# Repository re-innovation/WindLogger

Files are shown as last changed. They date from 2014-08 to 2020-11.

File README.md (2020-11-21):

# Low Cost Data Logger for Wind Speed Parameters
This repository has the open-source files for a Data Logger for Wind Speed and other small wind turbine parameters.

So far there have been two different versions of this unit:
* Version 1 was released in 2014. This was basic add on shield for the 'DataDuino' (an Arduino based SD card datalogger from www.re-innovation.co.uk)
* Version 2 was released on 2016. This was a surface mount design with additional functions such as solar PV charging.

The Wind Logger was originally designed by Matt Little of www.re-innovation.co.uk
Contact: info@re-innovation.co.uk

Please see: www.re-innovation.co.uk and search for 'wind datalogger' for more details.
Some more details are available here:
https://www.re-innovation.co.uk/docs/wind-datalogger/

The folders in this repository include:
	
* WindLogger_PCB
The PCB files were created in KiCAD PCB design software
These are in Windlogger_PCB
There are the KICAD project files and the GERBER files for both the DataDuino and the Windlogger Shield	

* WindLogger_FIRMWARE
Example code has been written for uploading via the Arduino IDE.

* WindLogger_FIXINGS
The CAD design for fixing system for an anemometer and a wind vane.
These is a work in progress. Originally draw using CorelDraw - I hope to update/convert this soon.
	
* WindLogger_INSTRUCTIONS
These are the instructions in a number of formats and languages.

## Version 1 - 2014
Overview of the design:
  A PCF8563 Real Time Clock is used to timestamp the data.

  Pin D3 is set up to cound pulses from a sensor (such as a anemometer or flow sensor)
 
  Pins D7,D8,D9 are set up to record digital information (0 or 1)
  
  Pins A0 to A3 are set up to record analogue information (0 to 1024)
  
  Each logger has a reference (user adjustable from 00-99).
  
  Data is written to a .csv file created on an SD card.
  
  A new file is created each day. If file alreay present then data is appended.
  
  The file name is created from the reference number and the date in the format:
  
  RXXDXXXX.csv, where RXX is the reference number and DXXXX is the date in the format DDMM. 
  
  Data is stored with human readable headers. Check the Arduino code for these.
  
  You can adjust the parameters of the device using serial commands. These parameters are stored in EEPROM.
  These are:
  * R??E - This will change the reference number to ??
  * T??????E - This will change the time to HHMMSS
  * D??????E - This will change the date to DDMMYY
  * S?????E - This will change the sample period to ????? seconds. Set to 00001 for 1 second data, set to 03600 for 1 hour data. (The minimum is 1 second data. The maximum is 99999 seconds)

## Version 3 - 2016
 
This newer version mainly covers a new circuit board which was designed as a surface mount design. The Code on this board has additional changes, but not too different functionality.

## Version 4 - 2020

This is work in progress. I'm trying to create a better PCB design which will also have WiFi and GPRS/2G connectivity for your data.

The wind speed logging unit is a plug in board onto a data-logging main unit.

##  Data Processing
These are programs to take the data on the SD card and produce nice graphs with it.
This is a work in progress.
https://github.com/re-innovation/CSVviewer

## Changes to do!

* PCF8563 - not accurate enough. Use DS3231 with temperature compensation.
* Add data upload via WiFi
* Add data upload via GPRS

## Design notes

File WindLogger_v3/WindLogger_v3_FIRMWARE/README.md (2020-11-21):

# WindLoggerVersion3 - Arduino Code

  See www.re-innovation.co.uk for information and construction details

  The DataDuino is an Arduino based SD card datalogger.
  A PCF8563 Real Time Clock is used to timestamp the data.

  The logger is based on the Arduino Uno (ATMEGA328P).
  This board option should be selected in the Arduino IDE for programming.

## Features
  Counts pulses from a sensor (such as a anemometer or flow sensor)
  These are pulses are averaged into a wind speed.
  
  We also keep a record of the maximum in the averaging period.
  For turbulence measurement 
  
  Each logger has a reference number (user adjustable).
  
  Data is written to a .csv file created on an SD card.
  
  A new file is created each day. If file already present then data is appended.
  The file name is created from the current date in the format DXXXXXX.csv, where DXXXXXX is the date in the format YYMMDD. 
  
  Data is stored with a human readable header line at the start of the file.

## Using the code

  The code is a standard Arduino application. You can place the repository inside your Arduino sketches directory. 

  In order to build the software, additional arduino libraries are required.
  
  ### Logger configuration

  In app.h, you can set which fields are recorded.
  Each field has a READ define (for example READ_TEMPERATURE).
  To enable recording of this field, set this define to 1.
  To disable recording of this field, set this define to 0.
  
  ### Adding new fields

  To add a new field to the logger software (for example pressure):
  1. Create a define in app.h that will enable/disable the new field (for example READ_PRESSURE)
  2. Create the module .cpp and .h files. In the .h file, define the headers, e.g.

  ```
  #if READ_PRESSURE == 1
  #define PRESSURE_HEADERS "Pressure mb, "
  #else
  #define PRESSURE_HEADERS ""
  #endif
  ```

  3. In sd.cpp:
    1. Add the header entry to the s_pstr_headers string in the desired position. Be sure to add a trailing slash as per the exisiting entries.
    2. Find the write_configurable_fields function.
      * Add the necessary lines of code to write the new data string to the accumulator.
      * Ensure you surround the new code with ifdef...endif for the field.
      * Ensure you include the line to add a comma before the data.
      For example:

  ```
  #if READ_PRESSURE == 1
  accum->writeChar(comma);
  PRESS_WritePressureToBuffer(accum);
  #endif

  ```

### Required libraries:
  ####[https://github.com/GreyGnome/EnableInterrupt](EnableInterrupt by Mike Schwager)

  On Arduino versions > 1.6.2 this library can be installed via the Library Manager. Search for 'EnableInterrupt' in the manager.

  The WindLogger software is built with EnableInterrupt v0.9.4. Later versions may not be supported.

  ####[https://github.com/greiman/SdFat](SfFat by William Greiman)

  Download the repository from GitHub and copy the 'SdFat' folder to your local Arduino libraries folder.

  ####[http://playground.arduino.cc/Main/RTC-PCF8563](RTC-PCF8563 by Joe Robertson)

  Follow the 'Download, install and import' instructions on that page.

  #### Libraries in this repository

  As an alternative to download the libraries individually, this repository contains suitable versions of each library. Unzip "3rd-party-libraries.zip" into your local Arduino libraries folder.

## Calibrate Mode

  In calibrate mode you can adjust the parameters of the device using serial commands.
  These parameters are stored in device EEPROM so they will be saved if the logger is turned off.
  
  The serial commands are:

  "T??????E"
  
  This will change the time to HHMMSS
  
  "D??????E"
  
  This will change the date to DDMMYY
  
  "S?????E"
  
  This will change the sample period to ????? seconds. Set to 00001 for 1 second data, set to 03600 for 1 hour data.
  The minimum is 1 second data. The maximum is 99999 seconds
  
  "R??E"
  
  This will change the logger reference to ??. 
  
  "OE"
  
  This will take the current reading and write it to the current offset.
  
  "V1???E" &  "V2???E"
  
  These select the two resistor values from the resistor potential divider.
  Values are in k Ohm.
  
  R1 is the top resistor, R2 is the lower resistor.
  
  "I???E"
  
  This sets the current gain value, in mV/A

  "W1E" or "W0E" 
  
  "W1E" sets the windwave potentiometer to be on the HIGH side of the potential divider.
  "W0E" sets the windwave potentiometer to be on the LOW side of the potential divider.

## Pin Assignments
  
  D0 - Rx Serial Data
  
  D1 - Tx Serial Data
  
  D2 - RTC interrupt (1 second pulses)
  
  D3 - Anemometer 1 (pulse interrupt) (& Power to External Unit - eg GSM)
  
  D4 - LED DATA output
  
  D5 - Anemometer 2 (pulse interrupt)
  
  D6 - Calibrate Switch (pull LOW to set)
  
  D7 - Rx_GSM
  
  D8 - Tx_GSM
  
  D9 - Card Detect (SD)
  
  D10 - Chip Select - SD card
  
  D11 - MOSI SD card
  
  D12 - MISO SD card
  
  D13 - SPI CLock SD card
  
  A0 - Wind Vane measurement with 10k pull-down
  
  A1 - Internal battery voltage measurement (from potential divider)
  
  A2 - External voltage measurement (with potential divider) 0-40V DC
  
  A3 - Current measurement
  
  A4 - SDA - I2C connection to RTC
  
  A5 - SCK - I2C connection to RTC

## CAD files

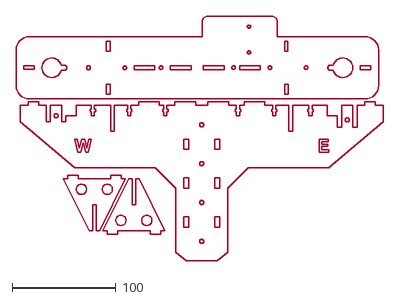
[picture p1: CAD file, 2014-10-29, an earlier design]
WindLogger_v1/WindLogger_v1_FIXINGS/2_10_14_Wind_Logger_Anemometer_Fixing_no_measurements.dxf
354.2 x 236.1

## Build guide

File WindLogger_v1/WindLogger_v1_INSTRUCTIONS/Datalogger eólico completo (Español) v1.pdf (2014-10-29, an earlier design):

### Datalogger eólico completo:

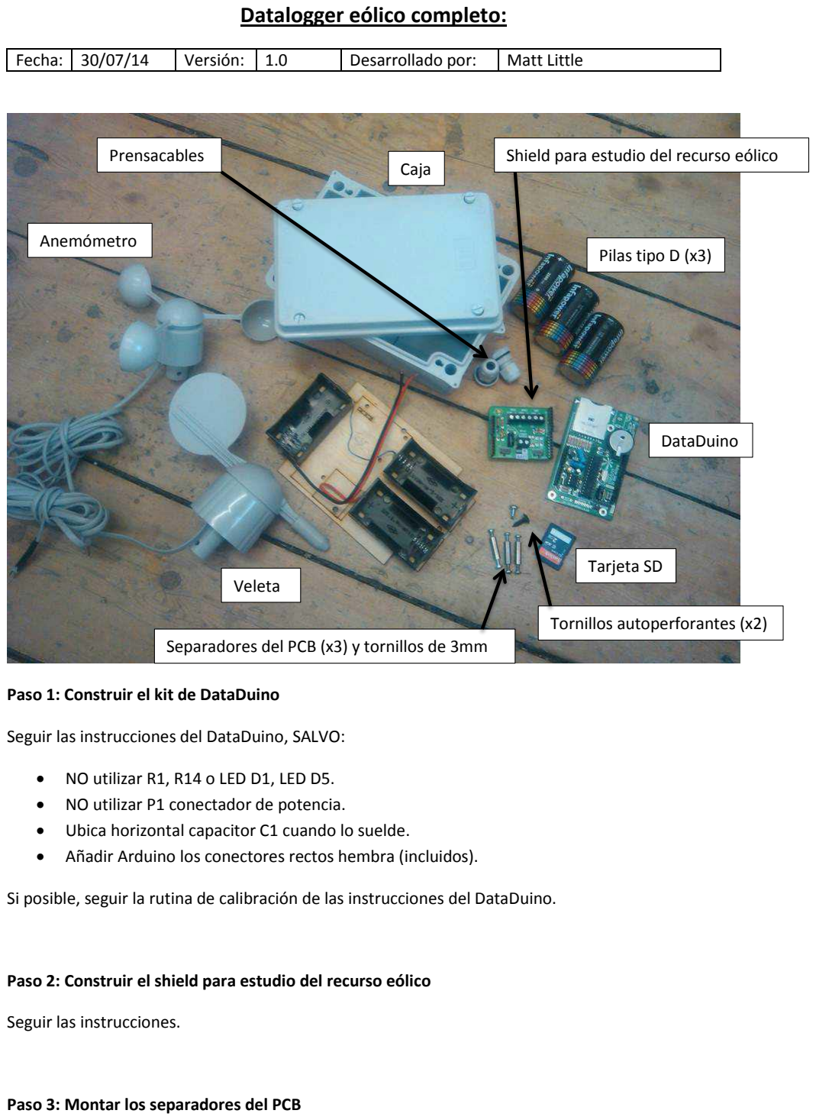
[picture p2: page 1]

Fecha: | 30/07/14 | Versión: | 1.0 | Desarrollado por: | Matt Little

Paso 1: Construir el kit de DataDuino

Seguir las instrucciones del DataDuino, SALVO:

- NO utilizar R1, R14 o LED D1, LED D5.
- NO utilizar P1 conectador de potencia.
- Ubica horizontal capacitor C1 cuando lo suelde.
- Añadir Arduino los conectores rectos hembra (incluidos).

Si posible, seguir la rutina de calibración de las instrucciones del DataDuino.

Paso 2: Construir el shield para estudio del recurso eólico

Seguir las instrucciones.

Paso 3: Montar los separadores del PCB

Caja

Anemómetro

Veleta

Pilas tipo D (x3)

Tarjeta SD

DataDuino

Prensacables | Shield para estudio del recurso eólico

Separadores del PCB (x3) y tornillos de 3mm

Tornillos autoperforantes (x2)

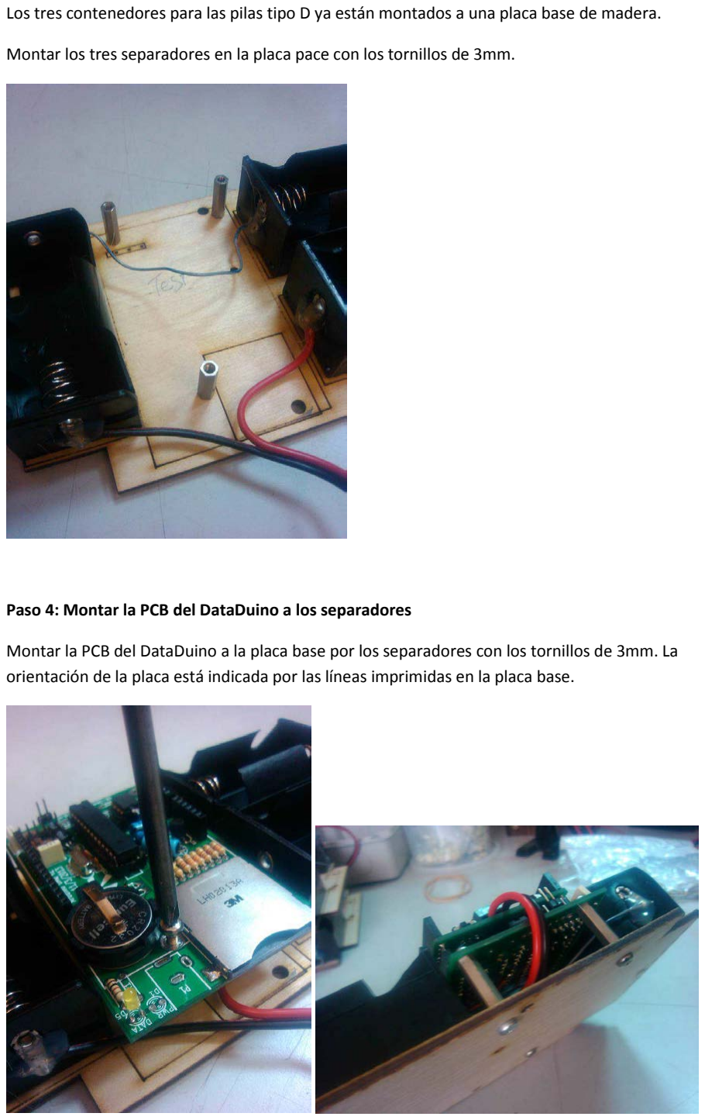
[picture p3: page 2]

Los tres contenedores para las pilas tipo D ya están montados a una placa base de madera.

Montar los tres separadores en la placa pace con los tornillos de 3mm.

Paso 4: Montar la PCB del DataDuino a los separadores

Montar la PCB del DataDuino a la placa base por los separadores con los tornillos de 3mm. La orientación de la placa está indicada por las líneas imprimidas en la placa base.

Paso 5: Montar el PCB del shield para estudio del recurso eólico

El shield para estudio del recurso eólico cabe encima del DataDuino con los conectores rectos hembra. Con cuidado, montarlo al DataDuino, asegurando que están bien alineados todos los conectadores.

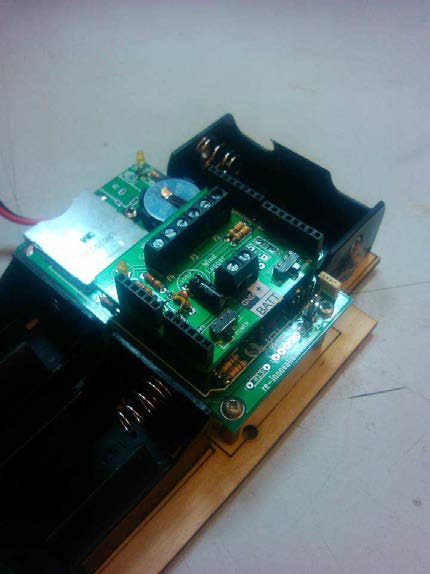
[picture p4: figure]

Paso 6: Conectar la potencia

Sacar 5mm de la aislante del cable de potencia rojo y negro de los tres contenedores de las pilas tipo D y conectarlo en el terminal de potencia (P1).

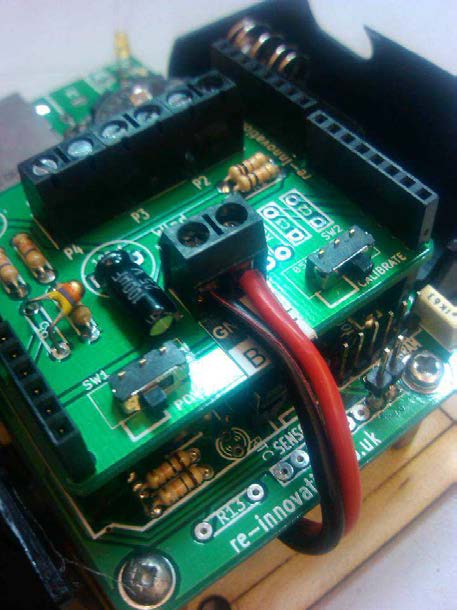
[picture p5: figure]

Paso 7: Montar los prensacables

Montar los prensacables en los agujeros en la caja. Asegurar que están bien apretados.

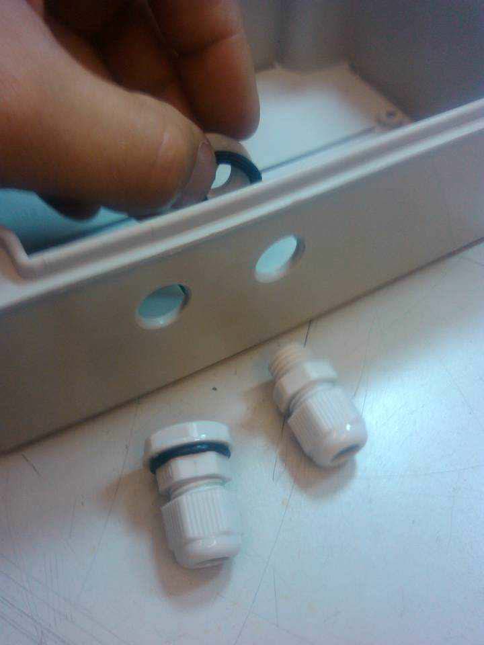
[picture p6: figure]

Paso 8: Introducir la tarjeta SD

Empujar la tarjeta para hacer que entra o sale del leedor de tarjetas SD.

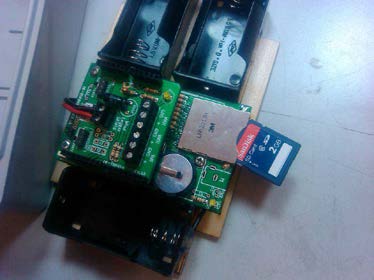
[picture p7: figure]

Paso 9: Montar la placa base en la caja

Montar la placa base de madera en la caja con dos tornillos autoperforantes. Uno tiene una cabeza ancha y entra por uno de los contenedores de pilas tipo D. El otro tiene una cabeza más delgada y cabe entre los dos otros contenedores de pilas.

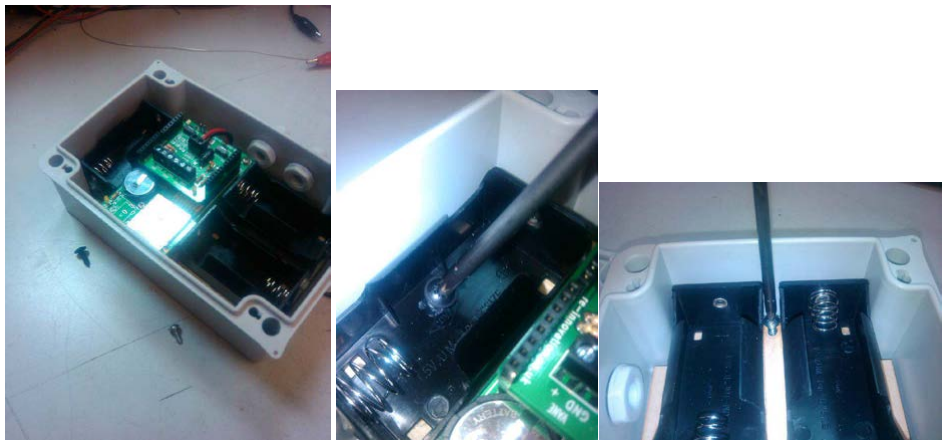
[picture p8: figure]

Paso 10: Conectar el anemómetro y veleta

Cortar los enchufes viejos del anemómetro y la veleta. Asegura que los cables entran por los prensacables.

El anemómetro tiene cables rojo y negro – saca la aislante y conectarlo al terminal Wind 1. La polaridad no importa.

La veleta tiene cuatro cables, pero solo el negro y la verde son necesarios – saca la aislante y conectarlo al terminal Vane. La polaridad no importa.

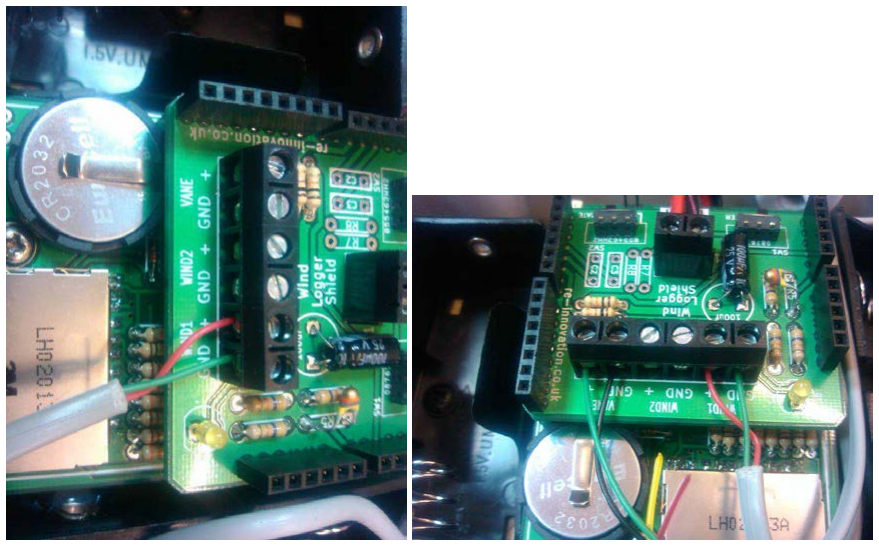
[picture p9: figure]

Paso 11: Poner a prueba con el cable FTDI

NO introducir las pilas. Encender el modo Calibrate (empujarlo el cambio Calibrate hacía el terminal BATT) y enchufar el cable FTDI.

Con una velocidad de transmisión de 115200, debería ver la palabra Calibrate en el terminal serial del IDE Arduino. Para más detalle, consultar las instrucciones del DataDuino.

Corregir la fecha, hora, numero de referencia y tiempo de medición.

Apagar modo Calibrate con el mismo cambio (empujarlo hacía los conectores rectos hembra) – el LED debería luminar una vez cada medición.

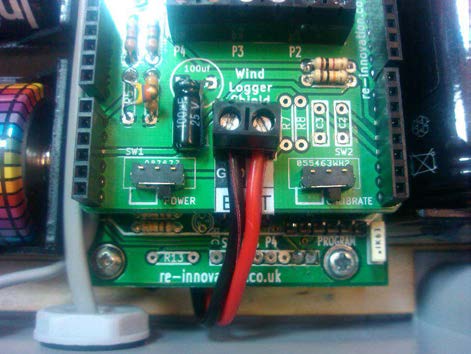
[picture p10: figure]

Paso 12: Introducir las pilas tipo D y encender

Sacar el cable FDTI y asegurar que las pilas tienen las polaridades correctas.

Encenderlo con el cambio Power (empujarlo hacía los terminales BATT)

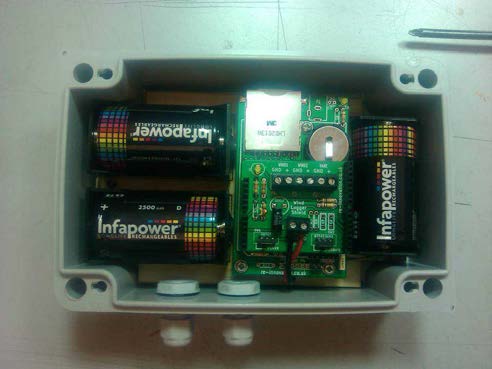
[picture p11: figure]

Paso 13: Instalar anemómetro y veleta

Asegurar que la veleta y anemómetro están instalados a una altura adecuada (si posible, a la misma altura que la turbina) y recordar esta altura.

Nivelar el anemómetro y veleta con un nivel

Orientar la veleta hacía el norte con sartén.

El anemómetro tiene factor de conversión de velocidad del viento a pulsos por segundo de 0.7m/s por Hz. Estos anemómetros no están calibrados en un túnel de viento.

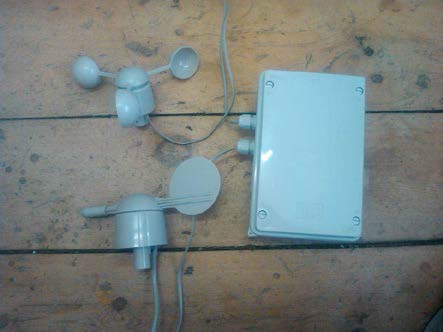
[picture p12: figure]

### Datos de contacto:

Este kit ha sido diseñado y producido por: Renewable Energy Innovation. info@re-innovation.co.uk
www.re-innovation.co.uk
Hopkinson Gallery
21 Street Station
Nottingham
NG7 6PD

Nos gustaría que este kit satisfaga sus necesidades. Si usted no estuviera satisfecho por algún motivo, por favor póngase en contacto con nosotros y le ayudaremos a solucionar el problema. Por favor escribanos a info@re-innovation.co.uk con cualquier pregunta o comentario que quiera hacer. Si falta alguna pieza de su kit por favor envíe un correo electrónico a info@re-innovation.co.uk con todos los detalles, incluyendo dónde se compró el kit.

Puedes encontrar más información técnica ingresando a nuestra web: www.re-innovation.co.uk

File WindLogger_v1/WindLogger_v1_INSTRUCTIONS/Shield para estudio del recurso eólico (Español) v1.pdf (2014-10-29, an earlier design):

### Shield para estudio del Recurso Eólico:

Fecha: | 29/07/14 | Versión: | 1.0 | Desarrollado por: | Matt Little

Este es un shield simple para implementar fácilmente un sistema de registro de datos del recurso eólico.
Está diseñado para leer 2 anemómetros mediante una
| | | | señal de pulsos y 1 veleta.

Está diseñado como Shield para ser montado en la placa principal DataDuino, que es una unidad de adquisición de datos Arduino que almacena datos en una tarjeta SD
| | | | (como un archivo .csv).

Las instrucciones siguientes muestran la construcción completa, incluyendo montaje en un gabinete estanco (no
| | | | suministrado por el kit).

Nota: Se requiere una placa DataDuino y una placa USB FTDI para conectar el cable serial para poder efectuar su
| | | | programación.

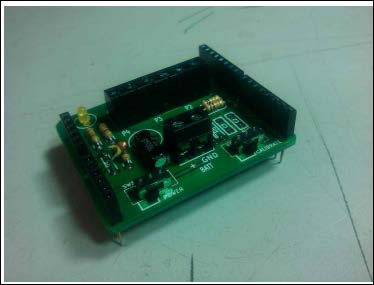
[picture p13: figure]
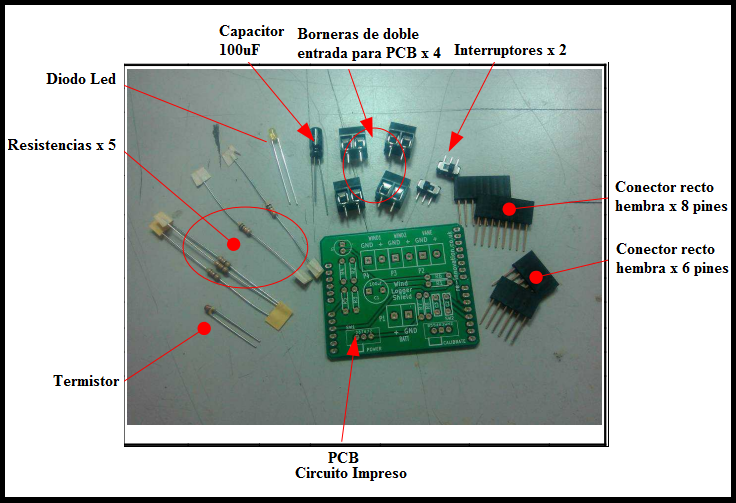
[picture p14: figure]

### Listado de Partes:

Referencia | Descripción | Referencia | Descripción
C1 | Capacitor electrolítico 100 uF | R1 | 10k
C2 | Capacitor Filtro (no incluido) | R2 | 47k
C3 | Capacitor Filtro (no incluido) | R3 | 47k
D1 | Diodo Led | R4 | 47k
P1 | Bornera de doble entrada | R5 | Termistor 47k NTC
P2 | Bornera de doble entrada | R6 | 1k
P3 | Bornera de doble entrada | R7 | Resistencia de Pull up (no incluida)
P4 | Bornera de doble entrada | R8 | Resistencia de Pull up (no incluida)
PCB | Circuito Impreso | SW1 | Interruptor de encendido “ON/OFF”
PINS | Conector recto hembra 8 pines x2 | SW2 | Interruptor de modo “Calibración”
PINS | Conector recto hembra 6 pines x2

También necesitarás (no incluido aquí):
- Construir una placa DataDuino. http://www.reinnovation.co.uk/web12/index.php/en/products-2/dataduino-arduino-dataacquisition-unit) (http://www.reinnovation.co.uk/web12/index.php/en/products-2/dataduino-arduino-dataacquisition-unit) (ver este link que es erróneo)
- Una computadora con el IDE de Arduino instalado.
- Un conector FTDI USB a cable serial con el código: TTL-232R-3V3, como el que se muestra a continuación:

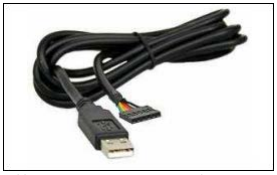
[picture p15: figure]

Lo puedes conseguir aquí (como en otros tantos lugares): http://www.ftdichip.com/Products/Cables/USBTTLSerial.htm

### Herramientas Requeridas:

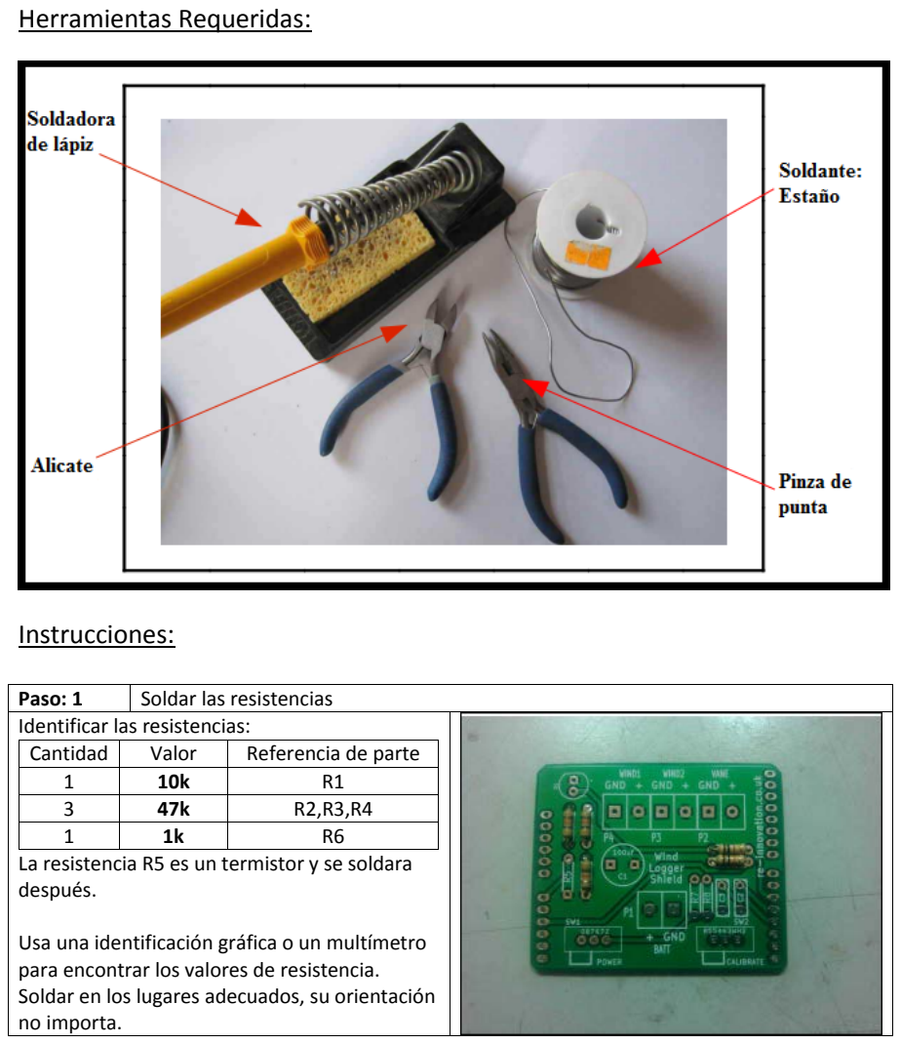
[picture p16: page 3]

### Instrucciones:

Paso: 1 | Soldar las resistencias
Identificar las resistencias:
Cantidad | Valor | Referencia de parte
1 | 10k | R1
3 | 47k | R2,R3,R4
1 | 1k | R6
La resistencia R5 es un termistor y se soldara después.

Usa una identificación gráfica o un multímetro para encontrar los valores de resistencia. Soldar en los lugares adecuados, su orientación no importa.

Paso: 2 | Soldar los 2 interruptores
| Colocar el interruptor de encendido donde dice “Power” y el de calibración donde dice “Calibrate” Asegúrese de que las palancas del interruptor apunten lejos del PCB.

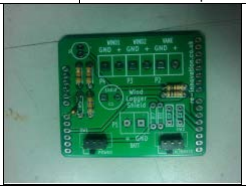
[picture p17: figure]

Paso: 3 | Soldar el diodo Led
Se puede efectuar un doble chequeo de la orientación del diodo led: Una forma es observando las patas, la larga es el positivo. La otra forma es observar el encapsulado del diodo led, el lado plano es el negativo. Asegúrate de hacer coincidir el lado plano con el diagrama blanco impreso en el PCB.
Paso: 4 | Soldar los capacitores

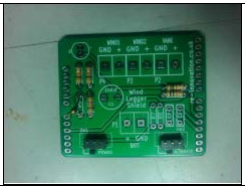
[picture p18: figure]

| Identificar y luego soldar los capacitores.
Cantidad | Valor | Referencia | Imagen
1 | 100uF | C1

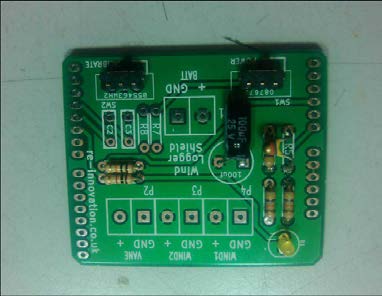
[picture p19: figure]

Comprueba la orientación en el capacitor C1. La línea blanca en un costado del capacitor marca el lado del negativo.
Hay 2 puntos de soldadura para C1 en el PCB, uno es el terminal redondo y se debe soldar allí el negativo, y en el terminal cuadrado el positivo.
Otra forma de conocer el positivo de C1 es reconocer la pata más larga.

Si es posible, doblar el capacitor para dejarlo apoyando en el circuito impreso.

Paso: 5 | Soldar el Termistor
Debemos soldar el termistor en los puntos de soldadura para R5. El Termistor puede sobresalir ligeramente de la placa para ayudar a sensar la temperatura del aire
Paso: 6 | Soldar las borneras

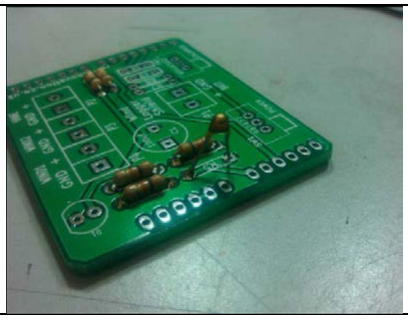
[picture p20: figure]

| Las borneras se enlazan con slots especiales. Enlazarlas para obtener 3 borneras en una fila. Asegurarse de que se coloquen en la dirección correcta: P2 / P3 / P4 y deben tener el frente hacia afuera del PCB. La bornera P1 debe colocarse con el frente hacia el otro lado del PCB.

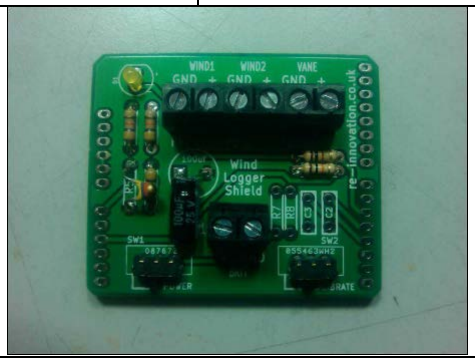
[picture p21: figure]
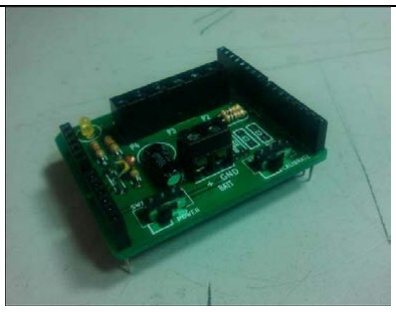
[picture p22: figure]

Paso: 7 | Soldar los pines de los conectores rectos hembra
Hay 2 conectores hembra de 6 pines y 2 de 8 pines. Coloque los pines del conector en el shield ya construido y luego presione hasta que pasen por el PCB para luego soldarlos al mismo. Esto ayuda a mantener todo recto y hace que sea más fácil montarlo en la placa base DataDuino. Resulta más fácil si ya se tiene un shield para utilizar como plantilla.

Paso: 8 | Colocar en la placa base DataDuino
| Este shield para estudio del recurso eólico debe encajar fácilmente en la placa base DataDuino (y también en otras placas que respetan el formato de Arduino).

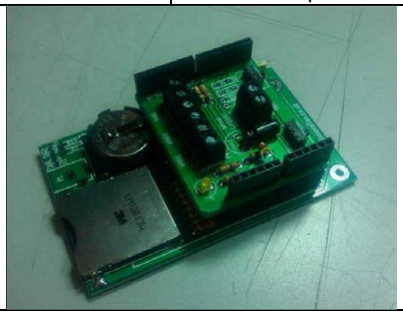
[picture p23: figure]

Paso: 9 | Cablear y colocar los soportes de las baterías y colocarlos en el gabinete
En el lote inicial de circuitos impresos que se mandaron a fabricar, la P1 BATT se marcó de forma incorrecta con + y GND invertidos. Para solucionar este error se colocó un sticker en todos los PCB con la correcta polaridad, por lo que se debe seguir esa indicación. Una placa de base cortada por láser fue diseñada para contener 3 pilas tipo D y los espaciadores de los circuitos impresos.

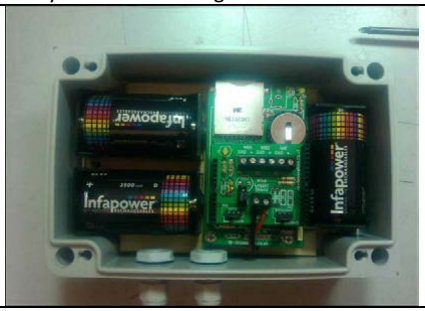
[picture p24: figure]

Paso: 10 | Efectuar el cableado desde los 2 anemómetros y la veleta
| Los anemómetros tiene una salida de señal tipo pulso, por lo que no importa la polaridad con la que se los conecte al shield. La veleta (en caso que se la utilice) tampoco importa la polaridad con la que se la conecte. Solo enciéndelo, establece la hora, fecha, referencia y periodo de muestreo y ya lo tienes!

### Datos de contacto:

Este kit ha sido diseñado y producido por: Renewable Energy Innovation. info@re-innovation.co.uk
www.re-innovation.co.uk
Hopkinson GallerY
21 Street Station
Nottingham
NG7 6PD
Nos gustaría que este kit satisfaga sus necesidades. Si usted no estuviera satisfecho por algún motivo, por favor póngase en contacto con nosotros y le ayudaremos a solucionar el problema. Por favor escribanos a info@re-innovation.co.uk con cualquier pregunta o comentario que quiera hacer.
Si falta alguna pieza de su kit por favor envíe un correo electrónico a info@re-innovation.co.uk con todos los detalles, incluyendo dónde se compró el kit.
Puedes encontrar más información técnica ingresando a nuestra web: www.re-innovation.co.uk

# Información útil:

## Circuito esquemático:

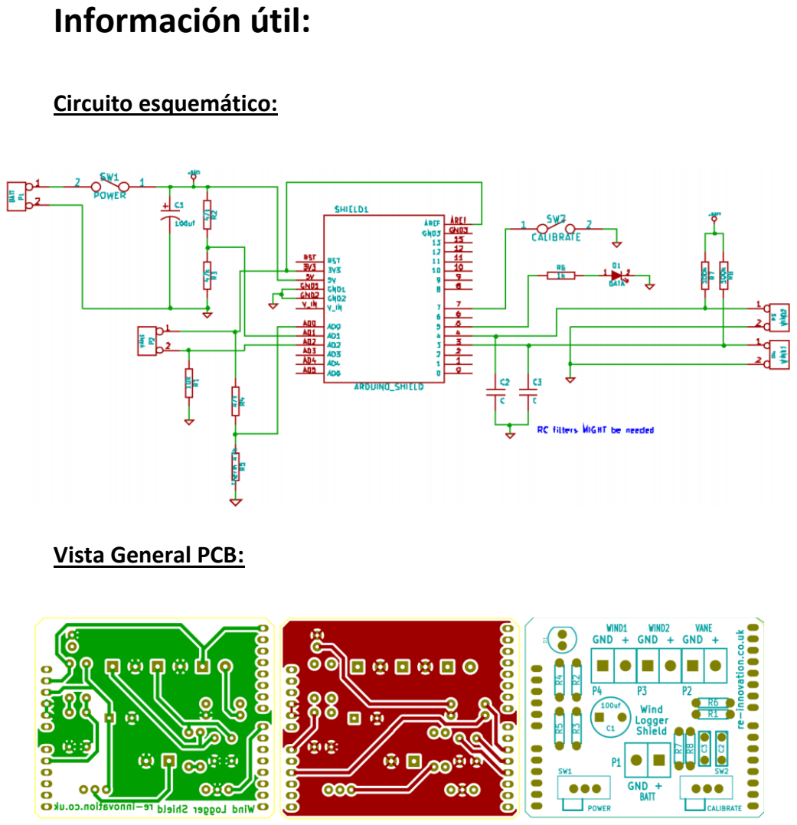
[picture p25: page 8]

## Vista General PCB:

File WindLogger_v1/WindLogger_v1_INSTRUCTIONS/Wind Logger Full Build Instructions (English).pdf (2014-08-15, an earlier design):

## Wind Resource Logger Unit

Date: | 30/07/14 | Version: | 1.0 | By: | Matt Little

These are instructions to put together a stand-alone remote wind resource logging system.
The unit is based upon the DataDuino (an Arduino based data logger) and a simple Wind Logger Shield.
It is designed to take inputs from two anemometers, a wind vane. It also records temperature and battery voltage. Data can be recorded at rates from 1 second to 99999 seconds. Generally 600 seconds (10 minutes) is used for wind speed measurements.

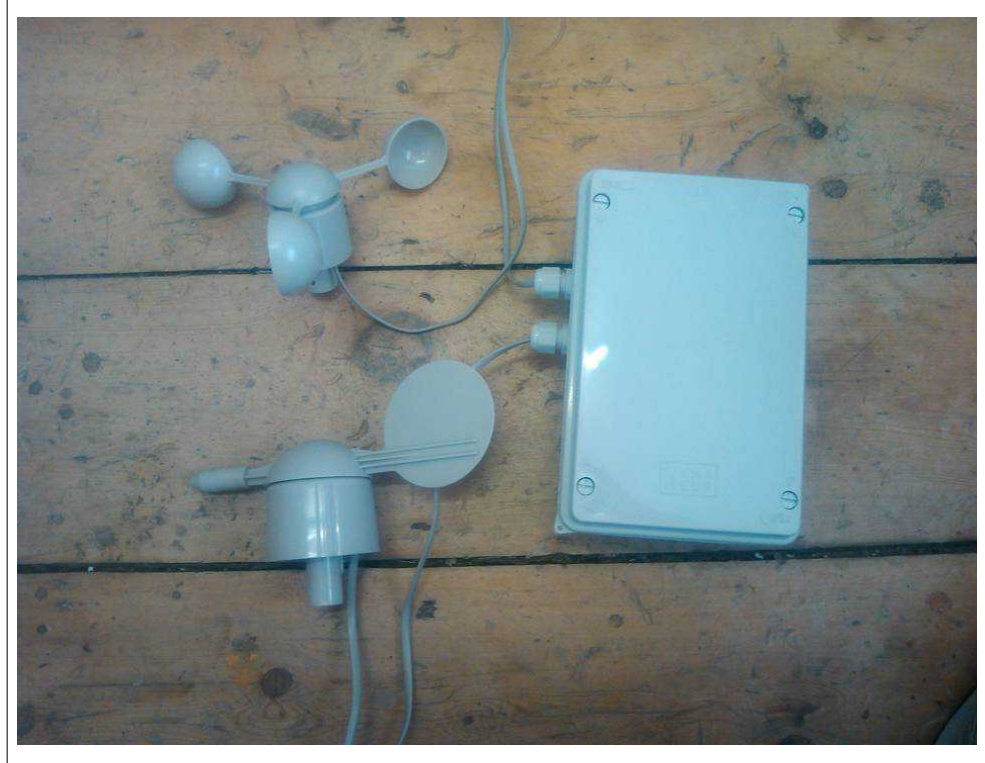
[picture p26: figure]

Please note that this kit is a work in progress – feedback is very welcome. Work on the Arduino code and data manipulation is in progress – please get involved.

This kit assumes knowledge of the Arduino IDE.

Note: These instructions assume you have:
- a DataDuino
- a Wind Logger Shield
You will also need an FTDI USB to serial cable for programming and an SD card for data storage.

Parts included:

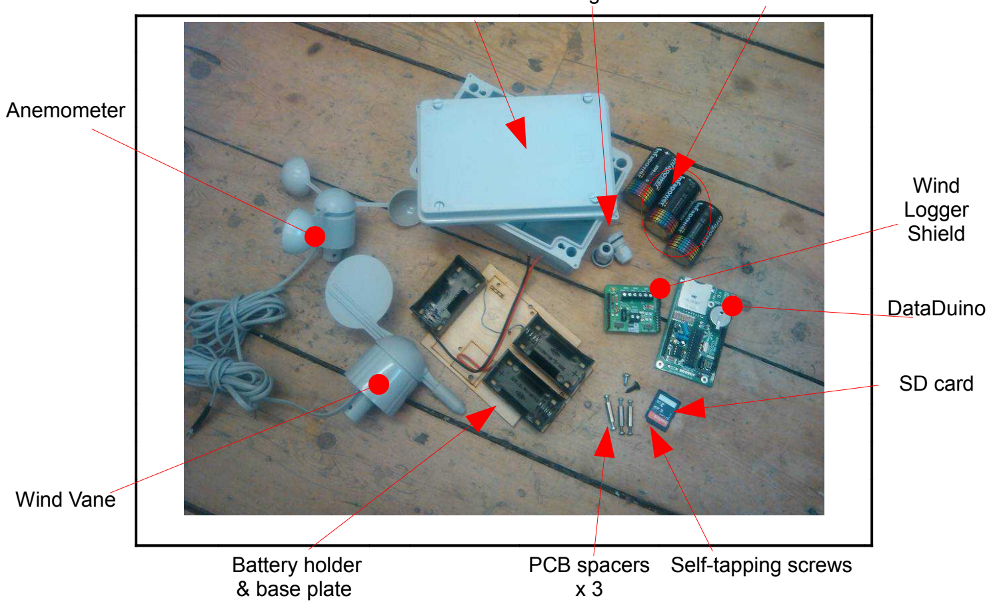
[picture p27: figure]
Anemometer; Wind Logger Shield; DataDuino; SD card; Wind Vane; Battery holder & base plate; PCB spacers x 3; Self-tapping screws

Enclosure Cable glands D cell batteries x 3

You will also need (not supplied):
- a computer with the Arduino IDE installed
- a FTDI USB to serial cable with code: TTL-232R-3V3, such as this:

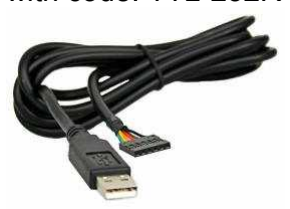
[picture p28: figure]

Available here (among other places): http://www.ftdichip.com/Products/Cables/USBTTLSerial.htm

Tools required:
- 3mm flat headed screwdriver
- 5mm flat headed screwdriver
- No 1. Posidrive screwdriver
- Wire cutters/strippers
- Pliers

Instructions:

Step: 1 | Build the DataDuino kit
Follow the instructions given with the DataDuino APART FROM: • Do NOT use R1, R14 or LED D1, LED D5. • Do NOT use P1 power connector • Lay C1 Capacitor flat when soldering. • Add the Arduino Shield Headers (included). If possible, follow the calibration routine given in the DataDuino instructions.
Step: 2 | Build the Wind Logger Shield
| Follow the instructions given.

Step: 3 Fit the PCB stand-offs The three D cell battery holders are already fixed to a laser cut base plate.

Using the three PCB stand-offs (these may be metal or plastic), fit them to the base plate through the 3 smaller cut-out holes. These use a 3mm screw through the base plate.

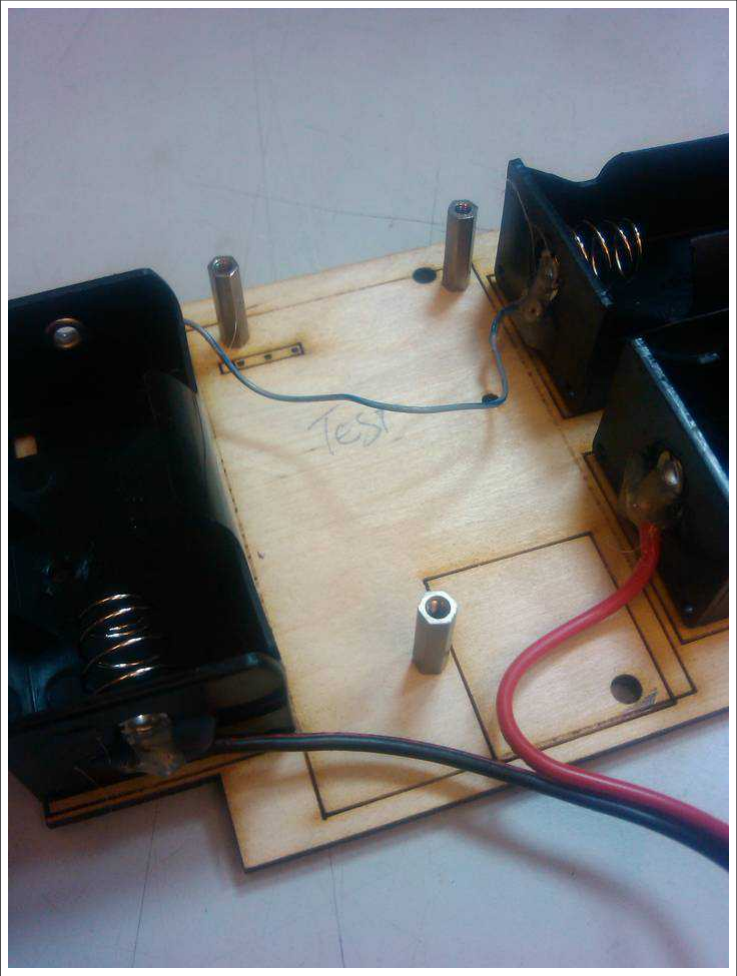
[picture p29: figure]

Step: 4 Fit the DataDuino PCB to the stand-offs Using three 3mm screws fit the DataDuino PCB to the PCB stand offs. The laser etched pattern will show which direction the PCB will fit.

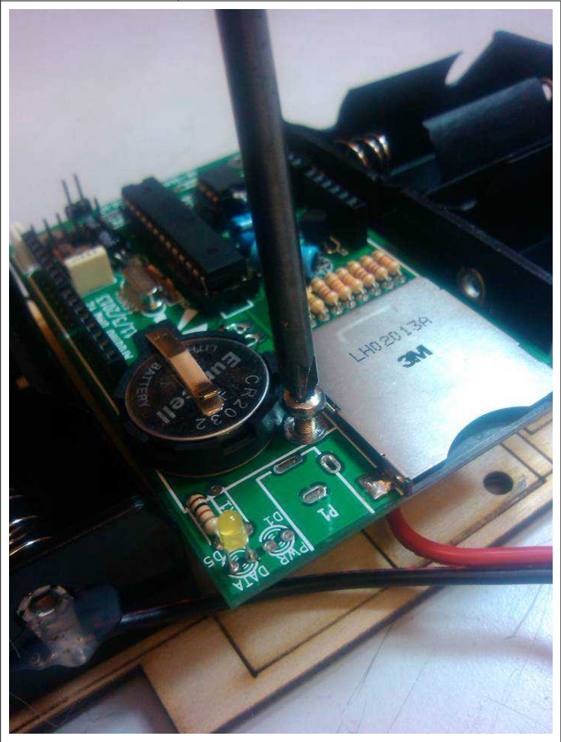
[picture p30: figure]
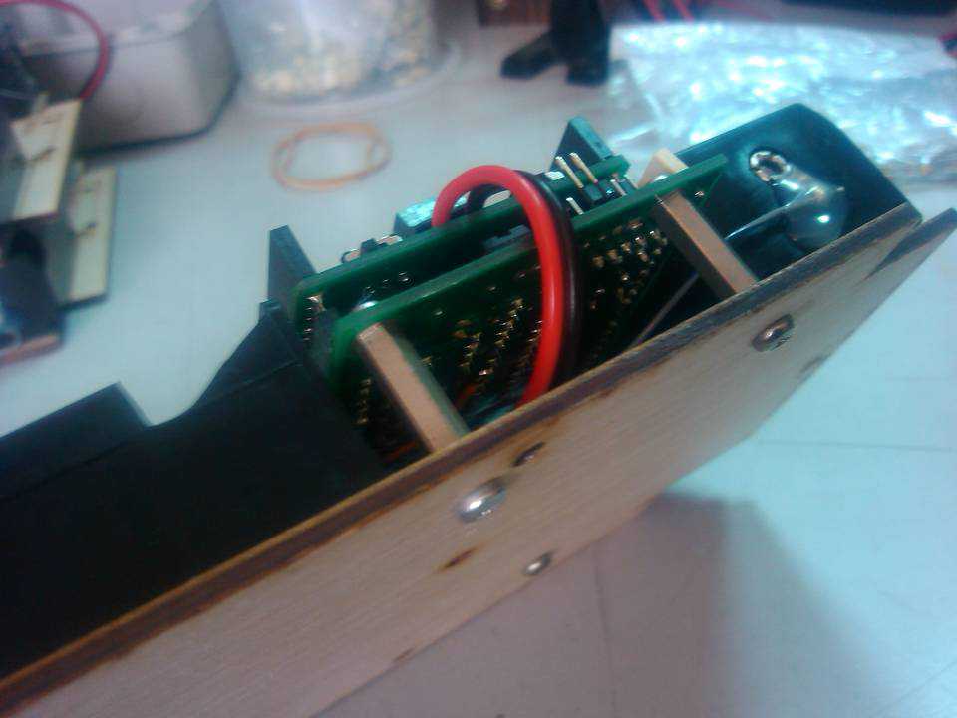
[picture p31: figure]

Step: 5 Fit the Wind Logger Shield PCB The wind logger shield fits onto the DataDuino using a number of header pins. Carefully fit this to the DataDuino ensuring all the pins are aligned.

Step: 6 | Wire up the power

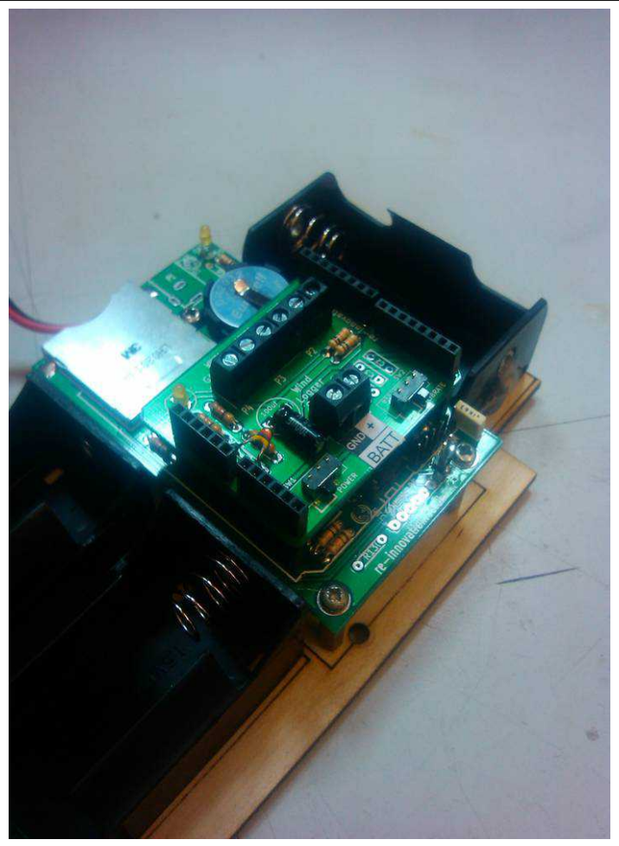
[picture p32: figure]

| The black/red power lead from the 3 x D cell battery holders needs to be stripped (around 5mm of insulation taken off). This can then be screwed into the 2 way power terminal block (P1).

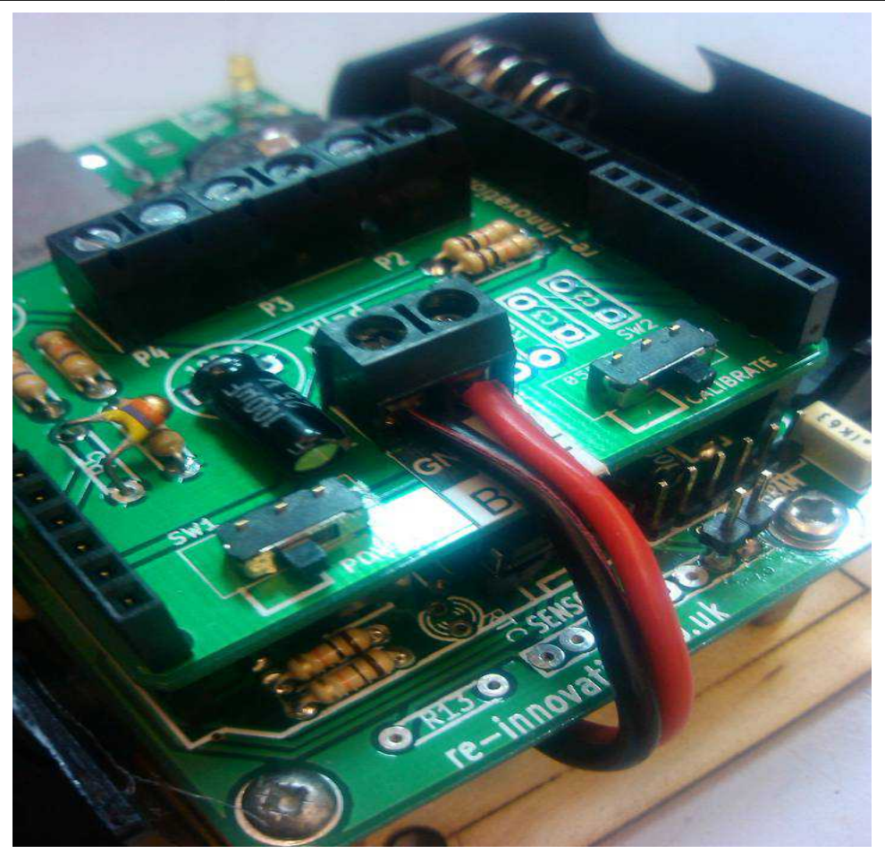
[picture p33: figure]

Step: 7 | Add the cable glands
These fit in the pre-drilled holes in the enclosure. Ensure they are well tightened up.
Step: 8 | Insert SD card

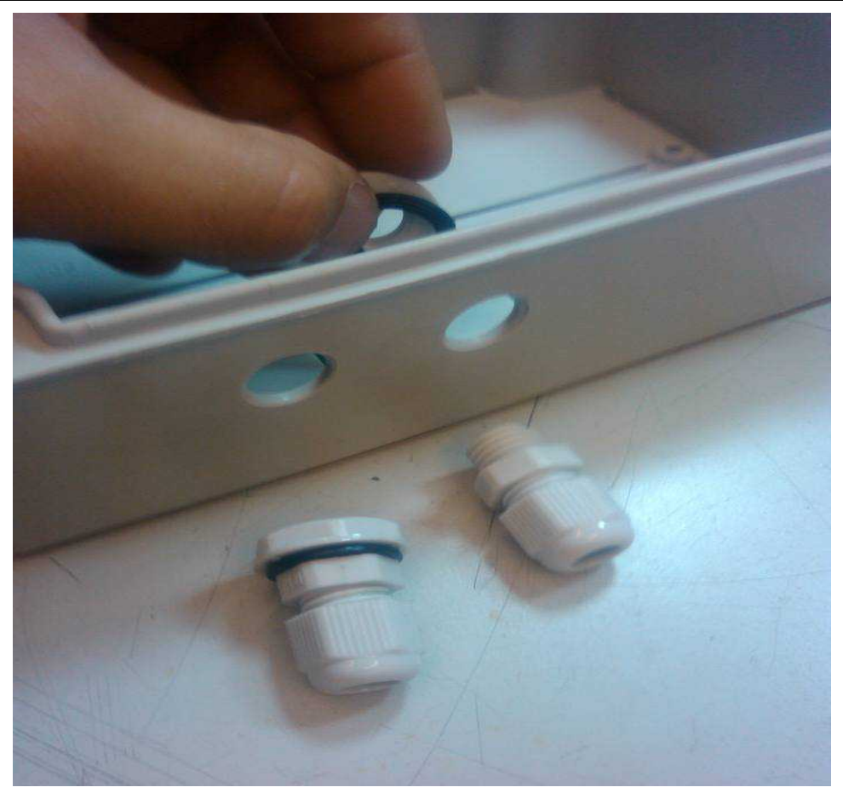
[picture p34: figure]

| This is a push to click in/push to click out type SD card holder.

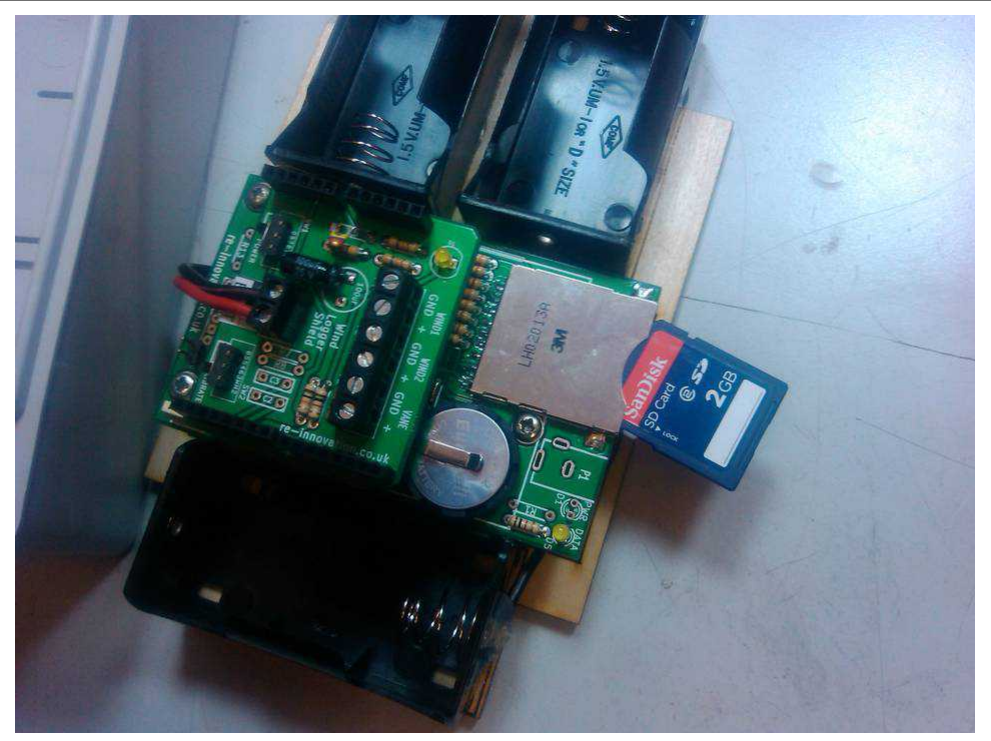
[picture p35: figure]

Step: 9 | Fit base plate into enclosure
The wooden base plate is
held in the enclosure with
two self-tapping screws.
One has a wide flat head
and goes through the
hole in the battery holder, the other has a narrower
head and goes in-between the two battery
holders.

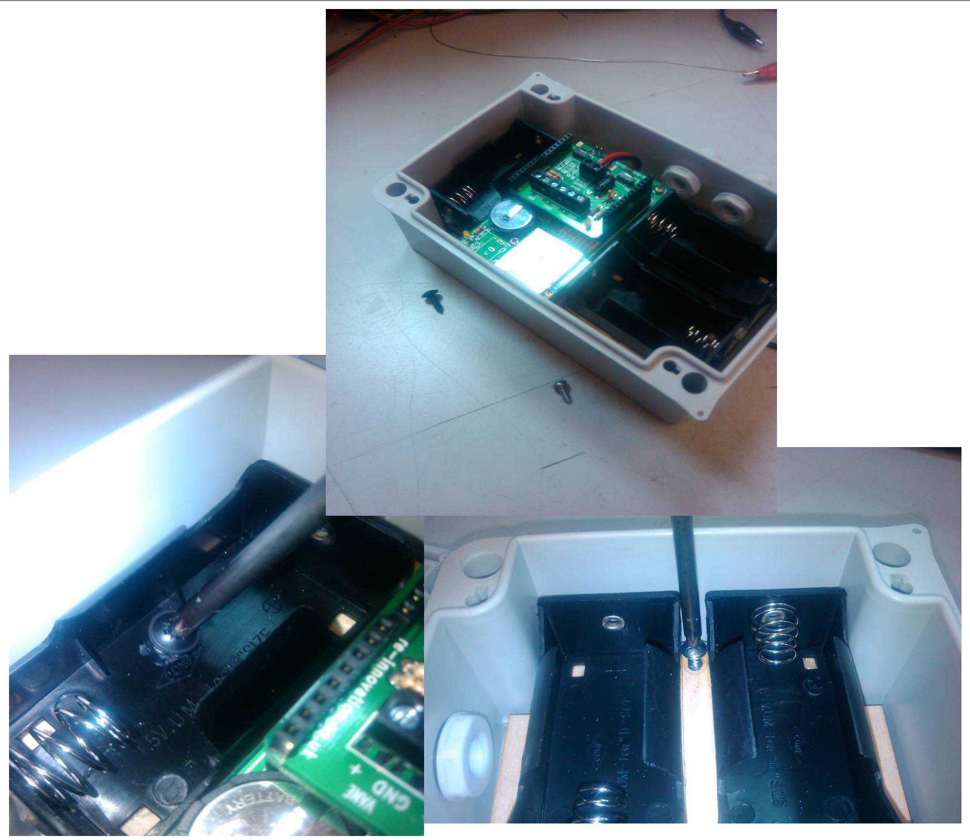
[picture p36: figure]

Step: 10 | Wire in Anemometer (x2) and Wind Vane The cables run through the cable gland. You will need to cut off the attached connector for the anemometer and wind vane.

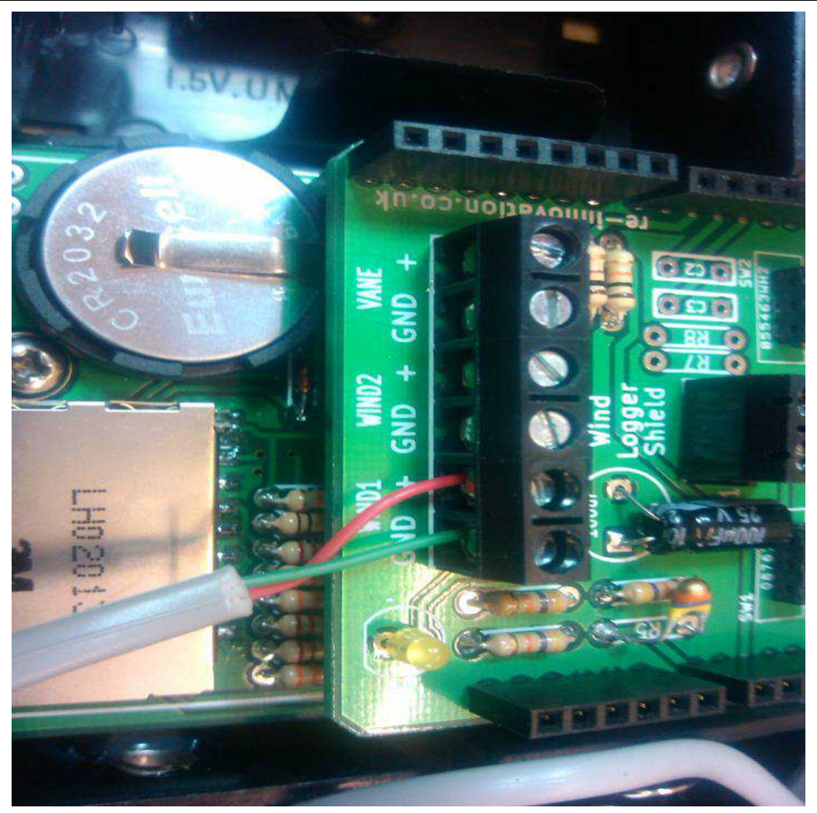
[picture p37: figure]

| The anemometer has a red and green cable – strip back and screw into the Wind 1/Wind 2 terminal blocks. Polarity does not matter.
| The wind vanes has four wires. You only need the black and the green cables. Screw into the Vane terminal. Polarity does not matter.

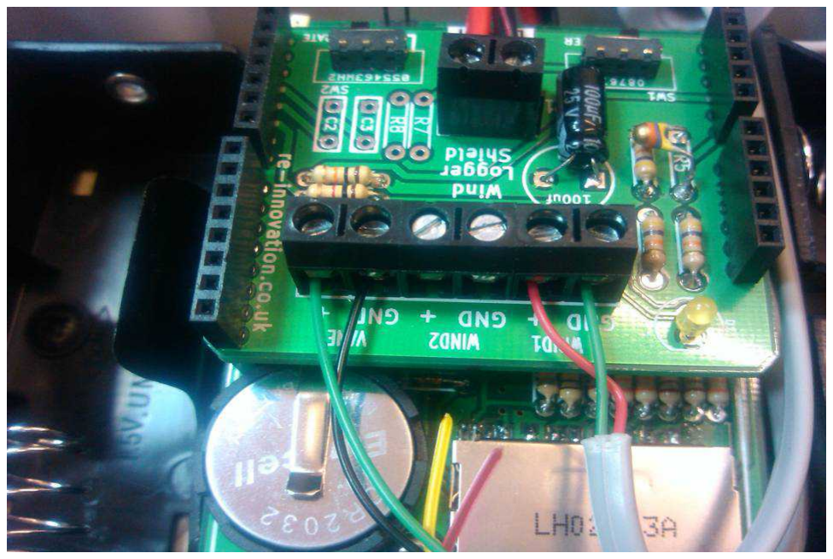
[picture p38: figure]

Step: 11 | Test using the FTDI cable
Do NOT insert batteries.
Set the Calibrate switch to ON (pushed towards the BATT terminal).
Plug in the FTDI cable.

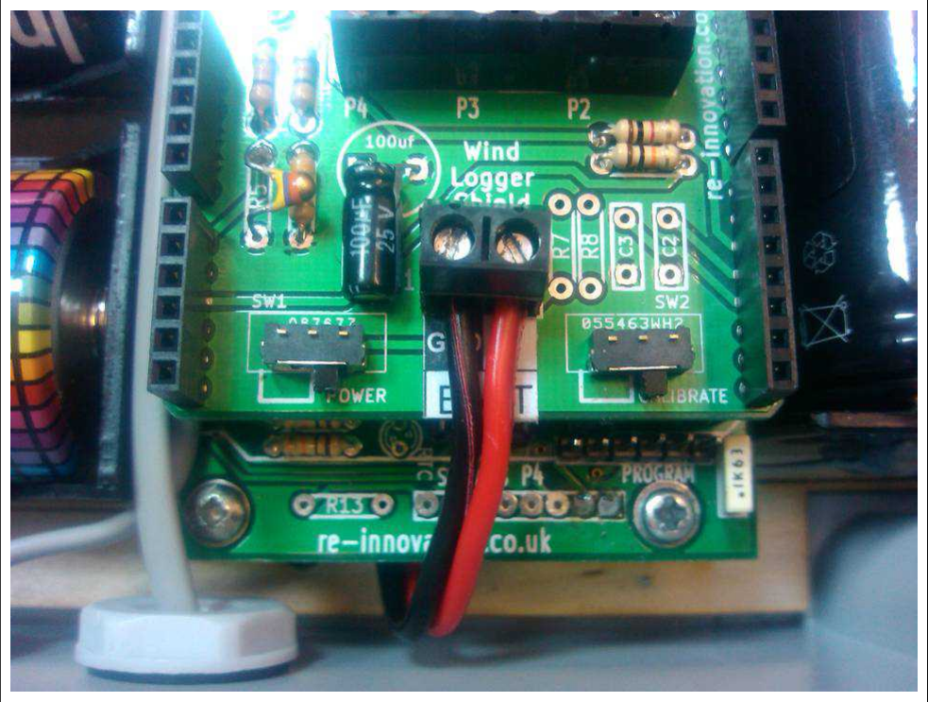
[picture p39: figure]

With a baud rate of 115200 you should see the word 'calibrate' on the serial terminal of the Arduino IDE.
Check the DataDuino instructions for more information.

Set the Date, Time, reference number and the sample period.

Switch Calibrate OFF (push towards the header pins on the side).
The LED should flash once every sample period.

Step: 12 | Place in D cell batteries and switch ON
| Remove the FTDI cable. Ensure correct polarity of the batteries. Power ON position is pushed towards the BATT connector

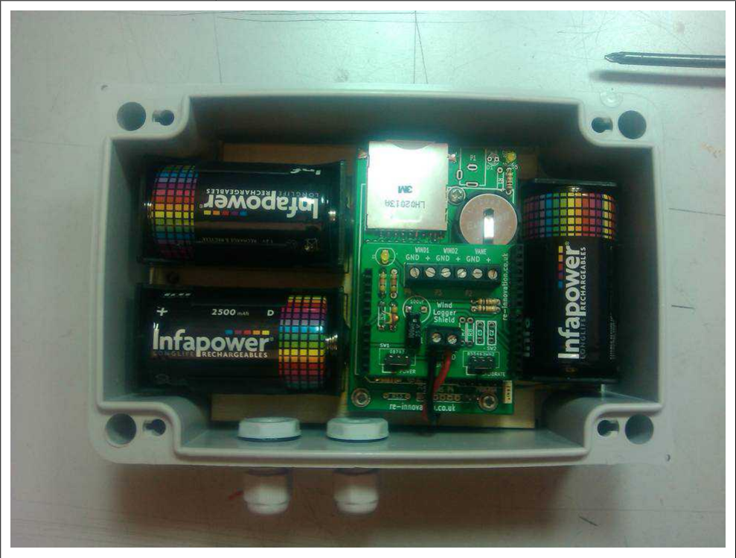
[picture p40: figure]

Step: 13 | Install Wind Vane and Anemometer
Ensure that the wind vane and anemometer are installed at a good height (if possible at the hub height of the wind turbine). Ensure the anemometer height is recorded. They must be installed level – use a spirit level to check this. The wind vane must be correctly oriented. Use a compass and the magnetic declination angle of the location to set north. (*** This is a work in progress ***). The anemometer frequency to wind speed coefficient is 0.7m/s per Hz. These anemometers are NOT calibrated.

Contact details:

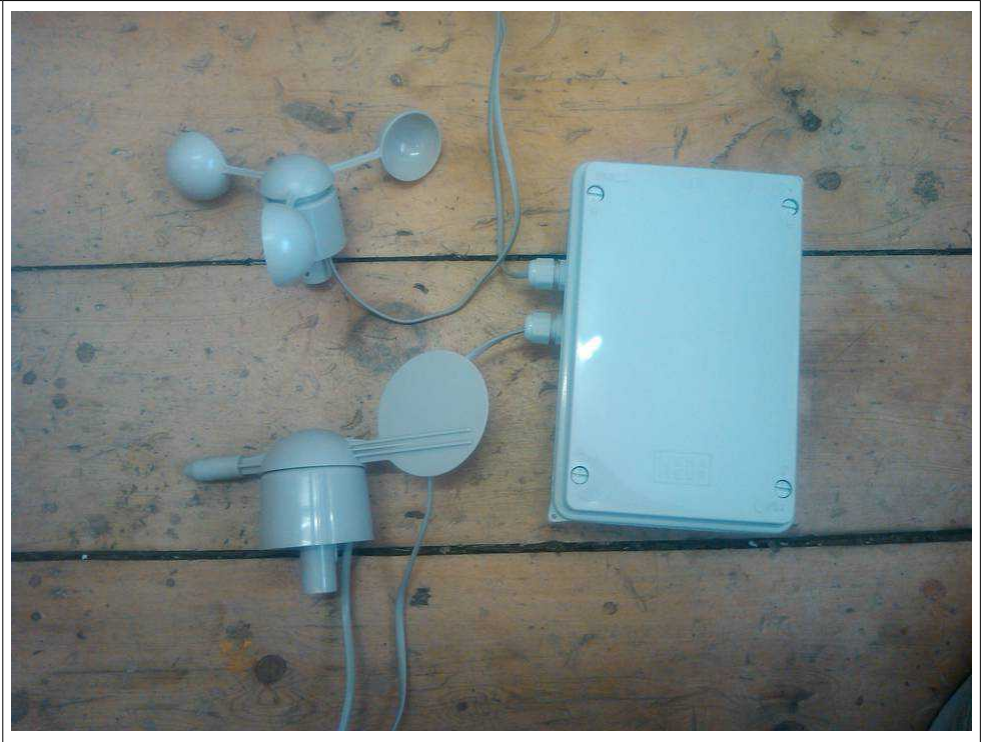
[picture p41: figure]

This kit has been designed and produced by: Renewable Energy Innovation. info@re-innovation.co.uk
www.re-innovation.co.uk
Hopkinson Gallery
21 Station Street
Nottingham
NG7 6PD

We would like you to be happy with this kit. If you are not happy for any reason then please contact us and we can help to sort it out. Please email info@re-innovation.co.uk with any questions or comments.
If any parts are missing from your kit then please email info@re-innovation.co.uk with details, including where the kit was purchased.

More technical information can be found via www.re-innovation.co.uk.

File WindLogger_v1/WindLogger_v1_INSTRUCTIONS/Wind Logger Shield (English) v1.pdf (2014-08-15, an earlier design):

## Wind Logger Shield

Date: | 29/07/14 | Version: | 1.0 | By: | Matt Little


This is a simple shield to easily implement a wind resource data logging system.
It is designed to read 2 x pulse type anemometers and 1 x wind vane.

It is designed as a shield to be added to the DataDuino, which is an Arduino data acquisition unit which stores data to an SD card (as a .csv file).

The instructions here show the full build, including mounting in a box (not supplied for the sheild kit).

Note: This requires a DataDuino and an FTDI USB to serial cable for programming.

Parts included:; 100uf Capacitor; Screw Terminals x 4; Switches x 2; LED; Resistors x 5; 8 way Header x 2; 6 way Header x 2; Thermistor; PCB

Parts list:

Reference | Description | Reference | Description
C1 | 100uf Electrolytic Capacitor | R1 | 10k
C2 | Filter capacitor (not included) | R2 | 47k
C3 | Filter capacitor (not included) | R3 | 47k
D1 | LED | R4 | 47k
P1 | 2 way screw terminal | R5 | Thermistor 47k NTC
P2 | 2 way screw terminal | R6 | 1k
P3 | 2 way screw terminal | R7 | Pull up resistor (not included)
P4 | 2 way screw terminal | R8 | Pull up resistor (not included)
PCB | | SW1 | ON/OFF power switch
PINS | 8 way header pins x 2 | SW2 | Calibrate mode switch
PINS | 6 way header pins x 2

You will also need (not supplied):
- a built DataDuino unit (http://www.re-innovation.co.uk/web12/index.php/en/products-2/dataduino-arduino-data-acquisition-unit) (http://www.re-innovation.co.uk/web12/index.php/en/products-2/dataduino-arduino-data-acquisition-unit)
- a computer with the Arduino IDE installed
- a FTDI USB to serial cable with code: TTL-232R-3V3, such as this:


Available here (among other places): http://www.ftdichip.com/Products/Cables/USBTTLSerial.htm

Tools required:

Side cutters; Small nosed; pliers

Soldering
Iron
Solder

Instructions:

Step: 1 | Solder the resistors
Identify all the resistors. You will have:
Quantity | Value | Part Reference
1 | 10k | R1
3 | 47k | R2,R3,R4
1 | 1k | R6


Resistor R5 is a thermistor and soldered later.

Use an identify chart or a multimeter to find the resistor values.
Solder into the relevant places.
Their orientation does not matter.

Step: 2 | Solder the switches
| Ensure the switch levers point away from the PCB.


Step: 3 | Solder the LED


Double check the LED orientation. The long lead is positive. The flat side of the LED body is negative – ensure this matches the PCB white diagram.

Step: 4 | Solder the capacitors
| Identify and then solder in the capacitors.


Quantity | Value | Reference | Photo
1 | 100uf | C1

Check the orientation on capacitor C1. The white line on the side signifies negative side. The round pad on the PCB signifies negative. The longer lead signifies positive. The square pad on the PCB is positive.

If possible, bend the capacitor to lie flat onto the PCB.

Step: 5 | Solder the Thermistor


This fits into the R5 pads. This can stick out from the board slightly to help monitor the temperature of the air.

Step: 6 | Solder the terminals
| The screw terminals link together with special slots – do this for the three in a row. Ensure they are facing the correct direction: P2/P3/P4 should face up away from the PCB, P1 should face down, away from the PCB.


Step: 7 | Solder the pin headers
There are 2 6-way headers and 2 8-way headers. It is easiest if you already have a shield to use as a template. Push the header pins on the already built shield and then push onto the PCB and solder. This helps keep them all straight and makes it easier to push into the DataDuino base.


Step: 8 | Fit onto the DataDuino base
| This shield should easily fit onto the DataDuino base (and also other Arduino shaped bases).


Step: 9 | Wire up to battery holders and fit into enclosure.
On the initial batch of PCBs the P1 BATT has been incorrectly marked with + and GND reversed. A sticker with the correct wiring has been put on all the PCBs, so follow that. A laser cut baseplate has been designed which holds 3 x D cell batteries, and the PCB spacers.


Step: 10 | Wire up the Anemometers & Wind Vane
| The anemometers are pulse output types, so do not matter polarity. The wind vane (if used) also does not matter about polarity. Power it up, set the time, date, reference and sample period and there you go!

Contact details:
This kit has been designed and produced by: Renewable Energy Innovation. info@re-innovation.co.uk
www.re-innovation.co.uk
Hopkinson Gallery
21 Station Street
Nottingham
NG7 6PD

We would like you to be happy with this kit. If you are not happy for any reason then please contact us and we can help to sort it out. Please email info@re-innovation.co.uk with any questions or comments.
If any parts are missing from your kit then please email info@re-innovation.co.uk with details, including where the kit was purchased.

More technical information can be found via www.re-innovation.co.uk.

## Useful Information:


Circuit schematic:

PCB overview:

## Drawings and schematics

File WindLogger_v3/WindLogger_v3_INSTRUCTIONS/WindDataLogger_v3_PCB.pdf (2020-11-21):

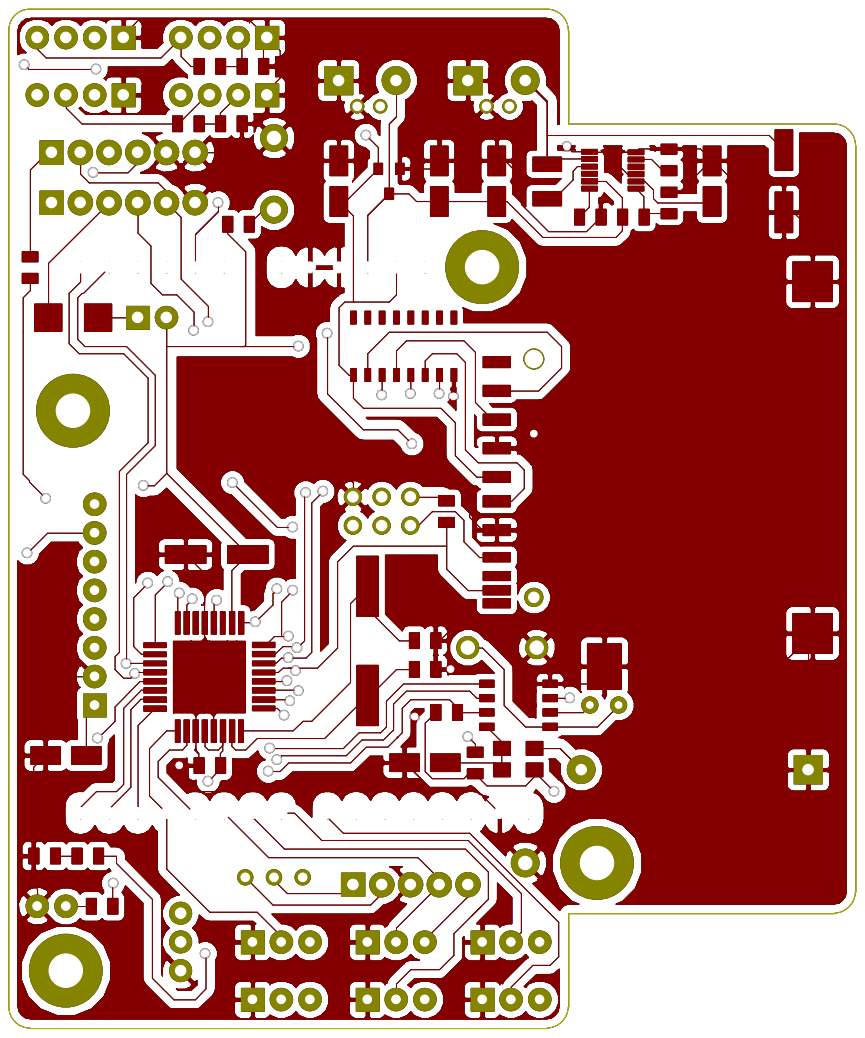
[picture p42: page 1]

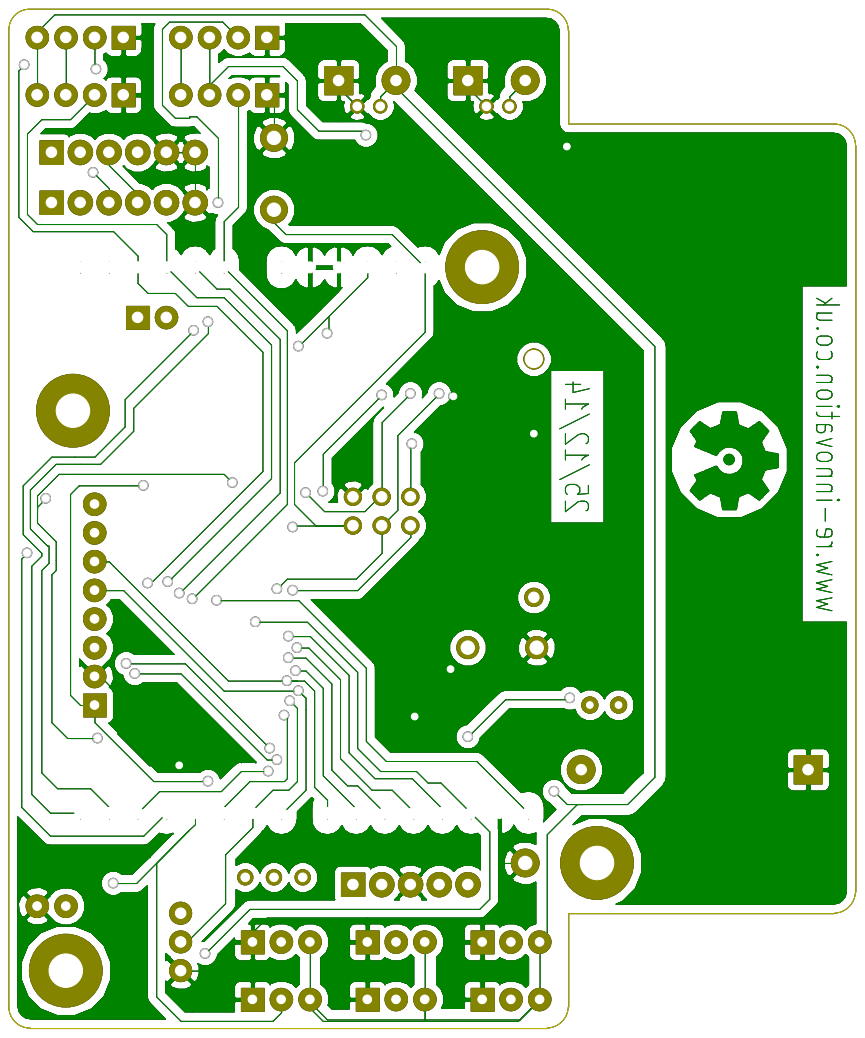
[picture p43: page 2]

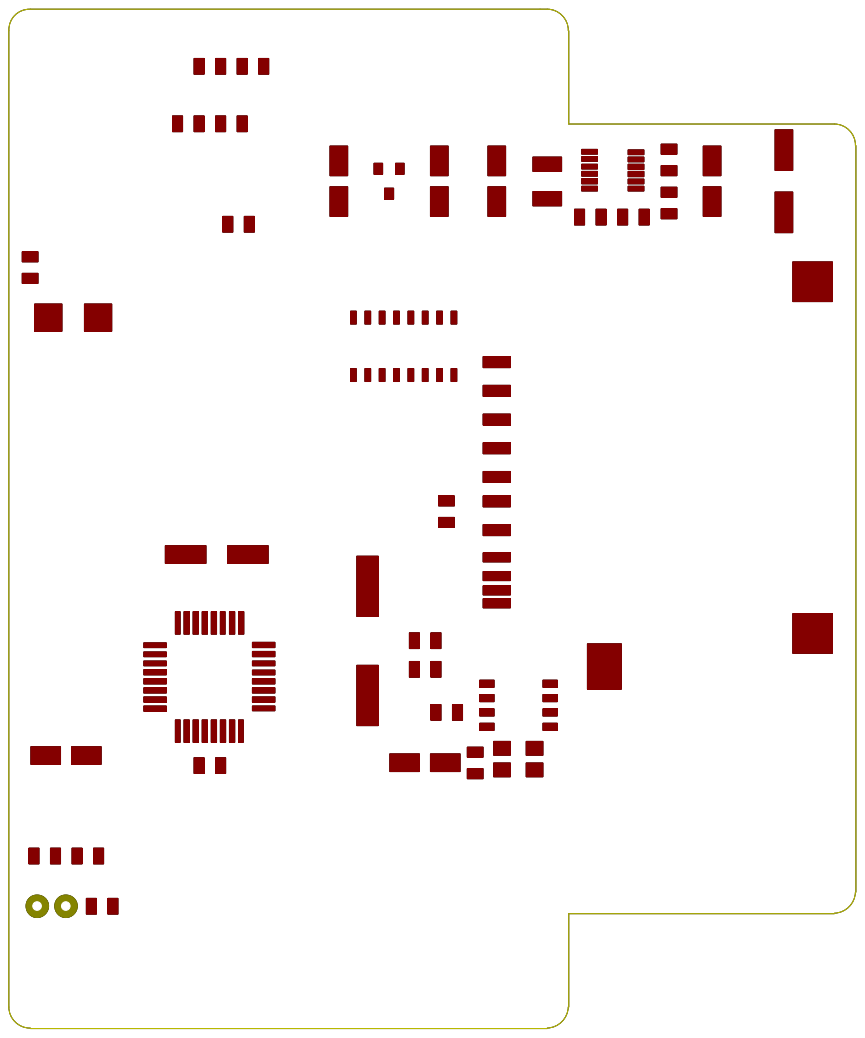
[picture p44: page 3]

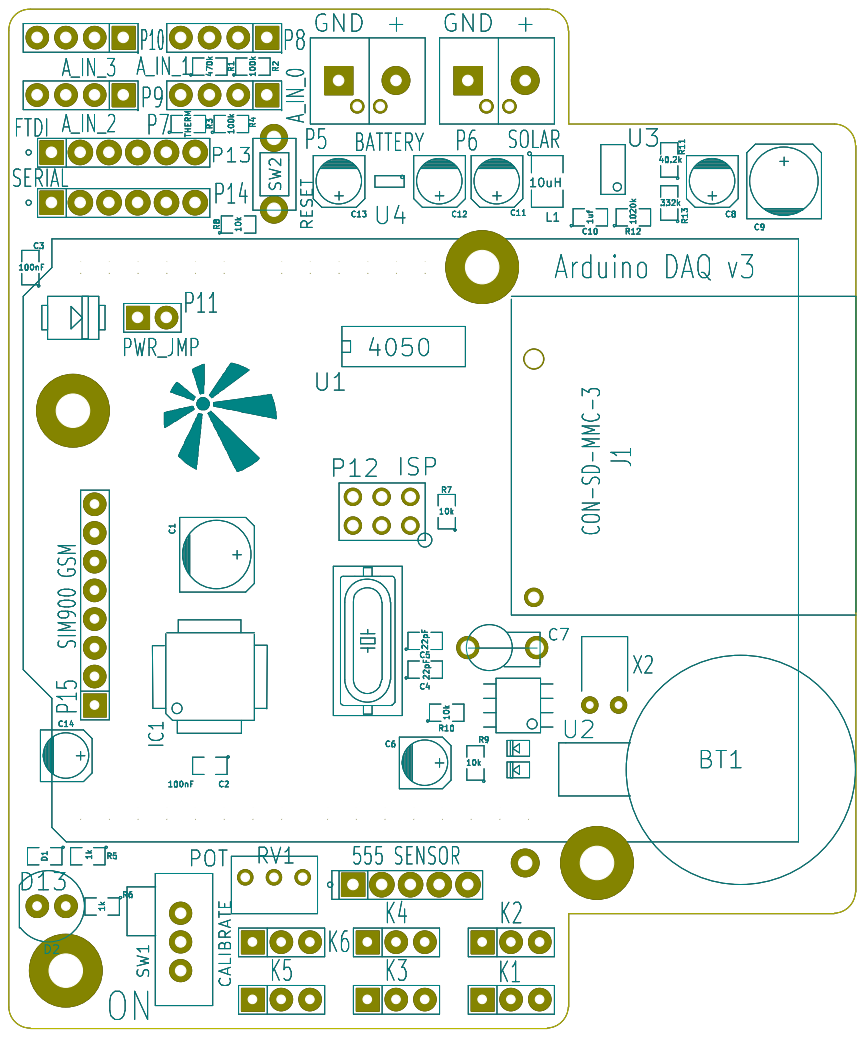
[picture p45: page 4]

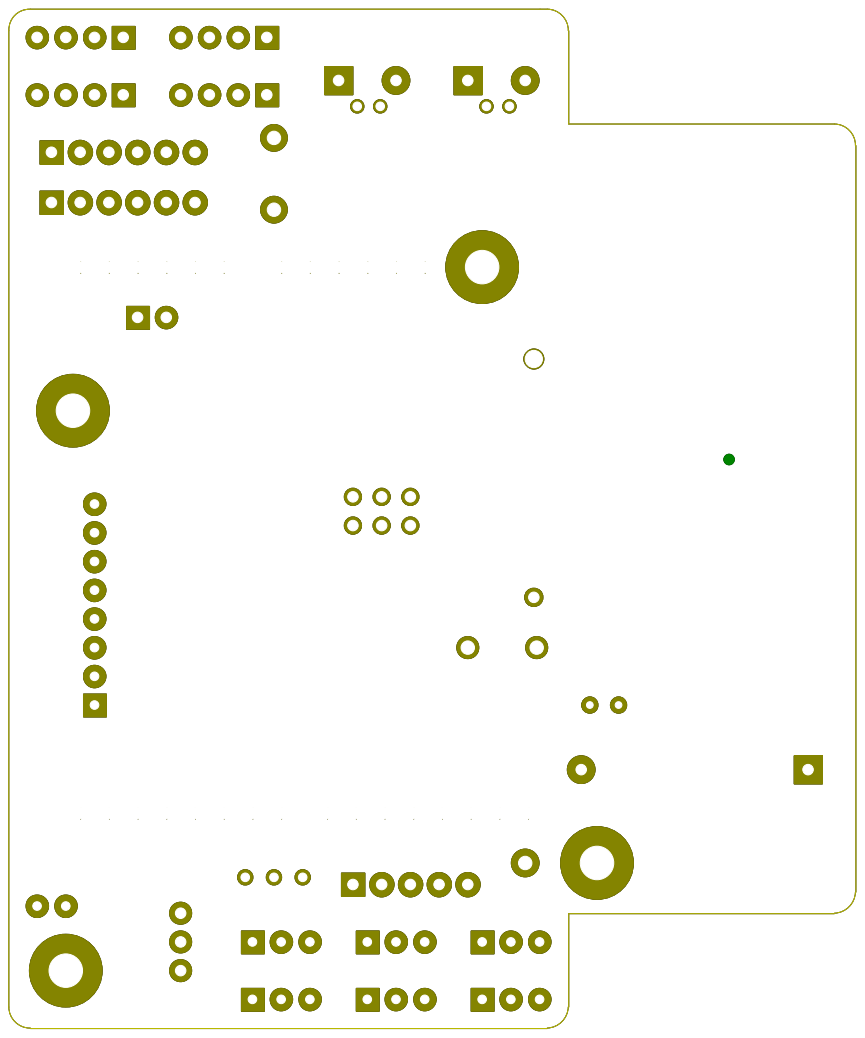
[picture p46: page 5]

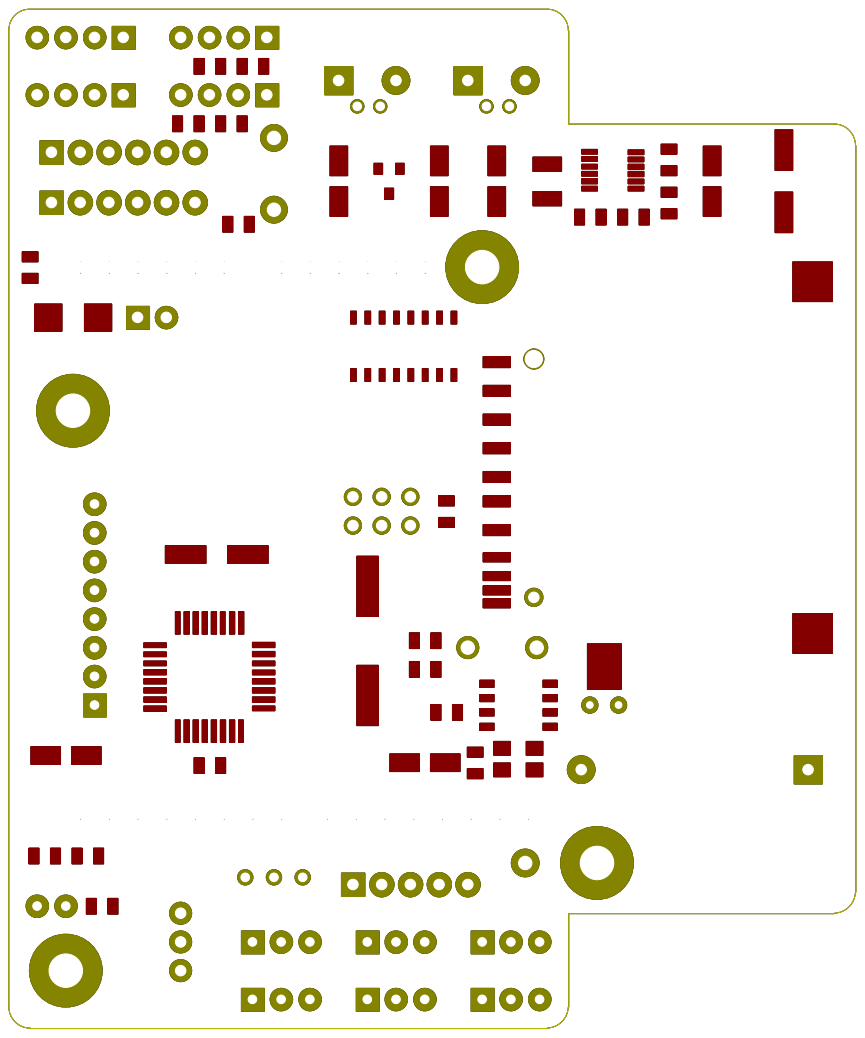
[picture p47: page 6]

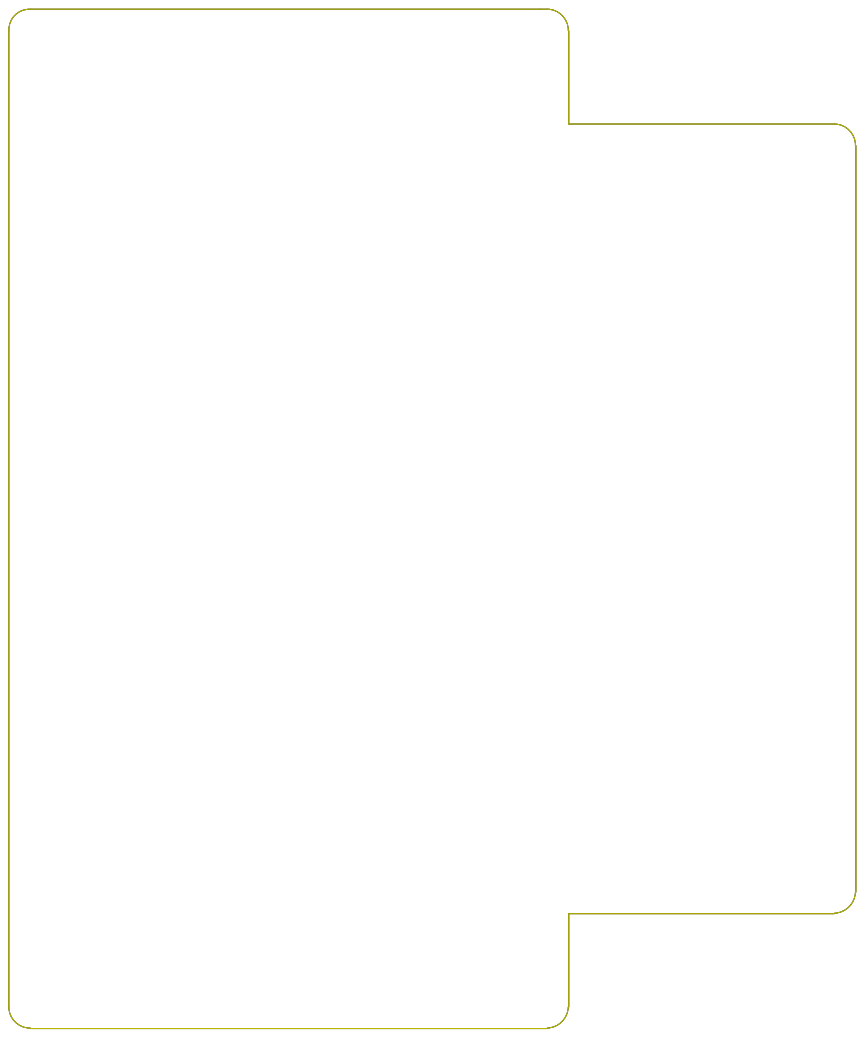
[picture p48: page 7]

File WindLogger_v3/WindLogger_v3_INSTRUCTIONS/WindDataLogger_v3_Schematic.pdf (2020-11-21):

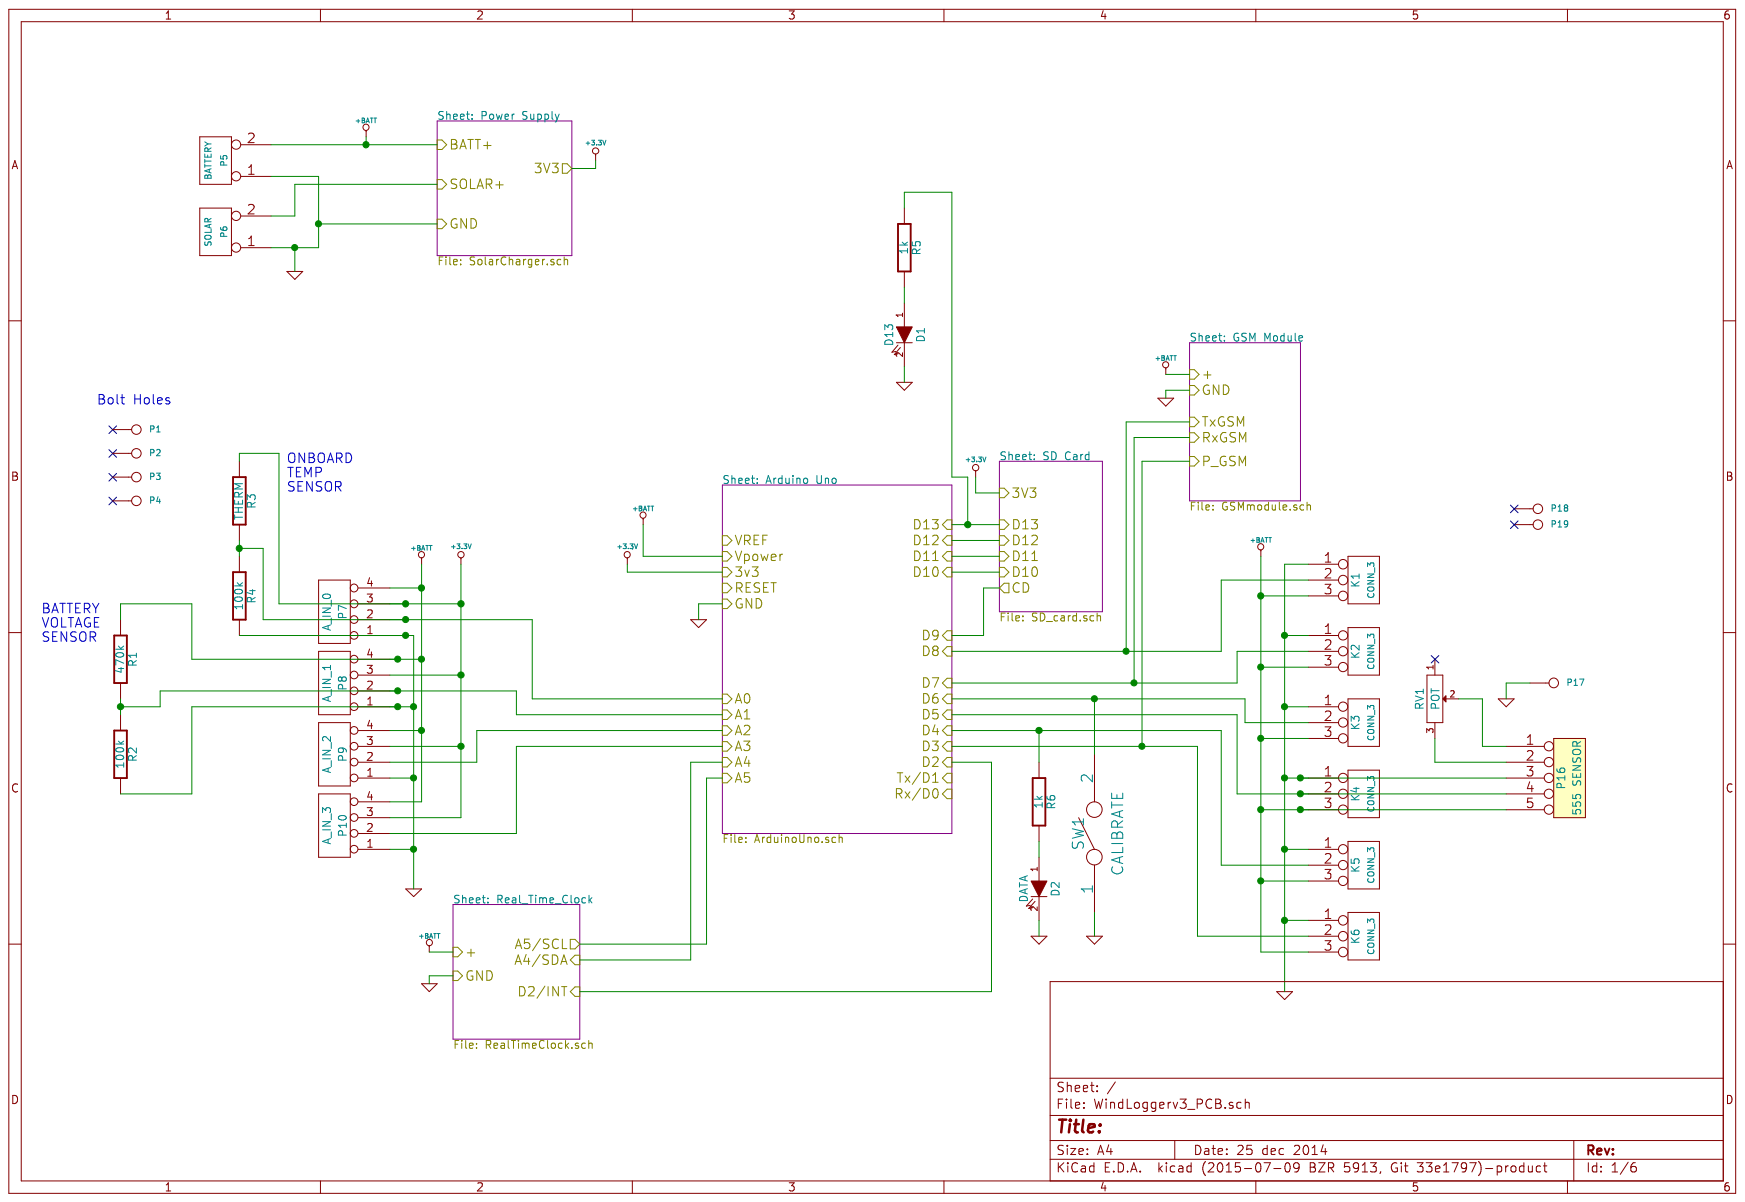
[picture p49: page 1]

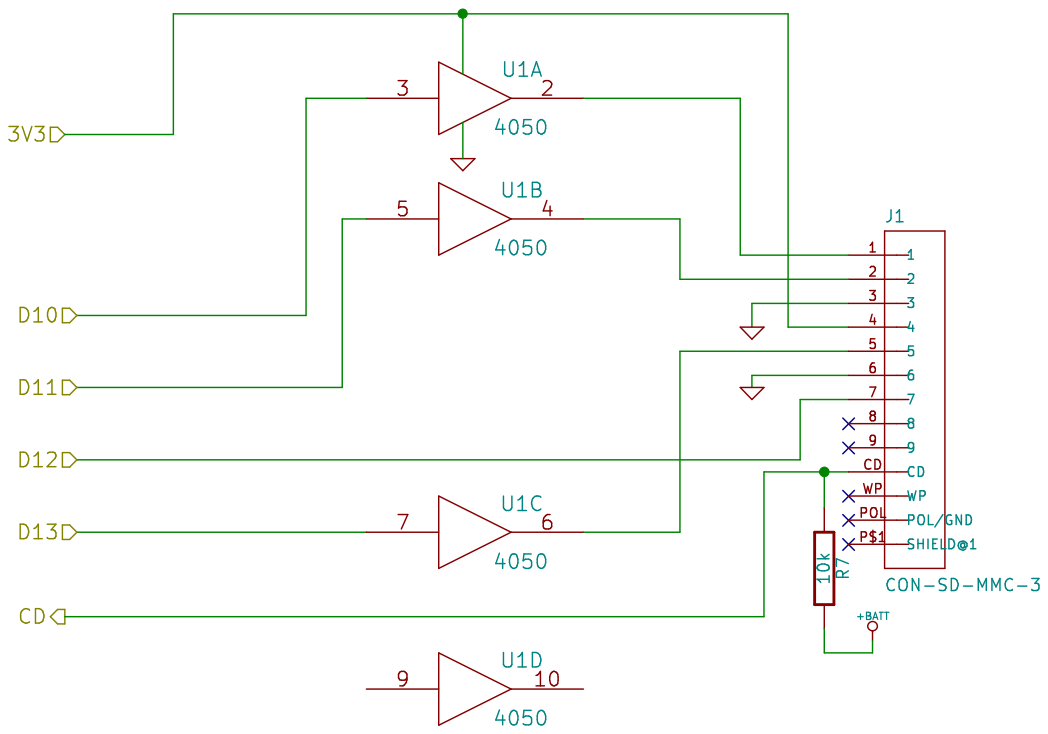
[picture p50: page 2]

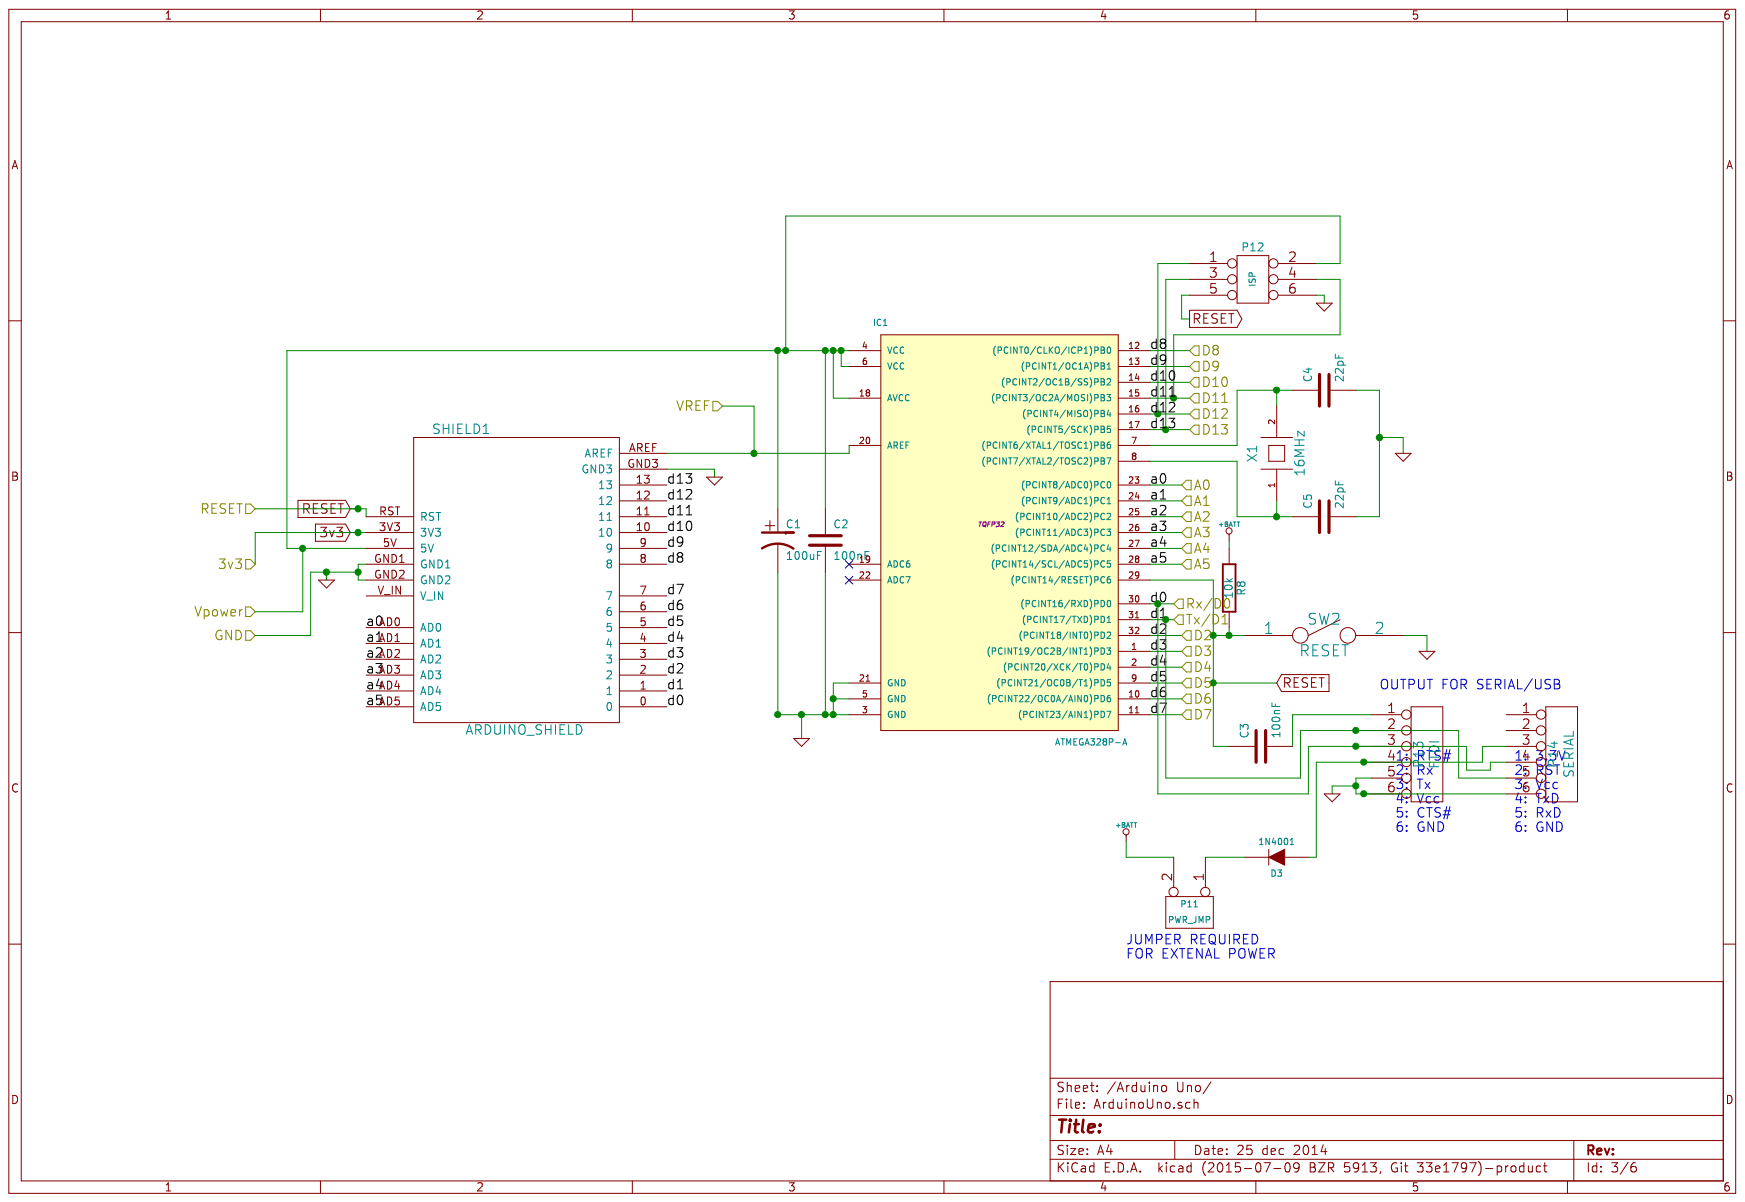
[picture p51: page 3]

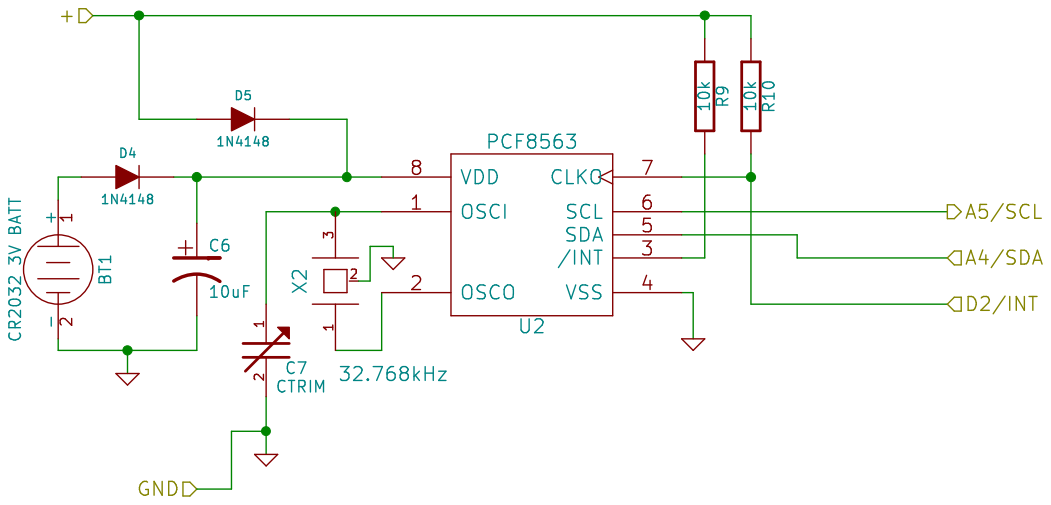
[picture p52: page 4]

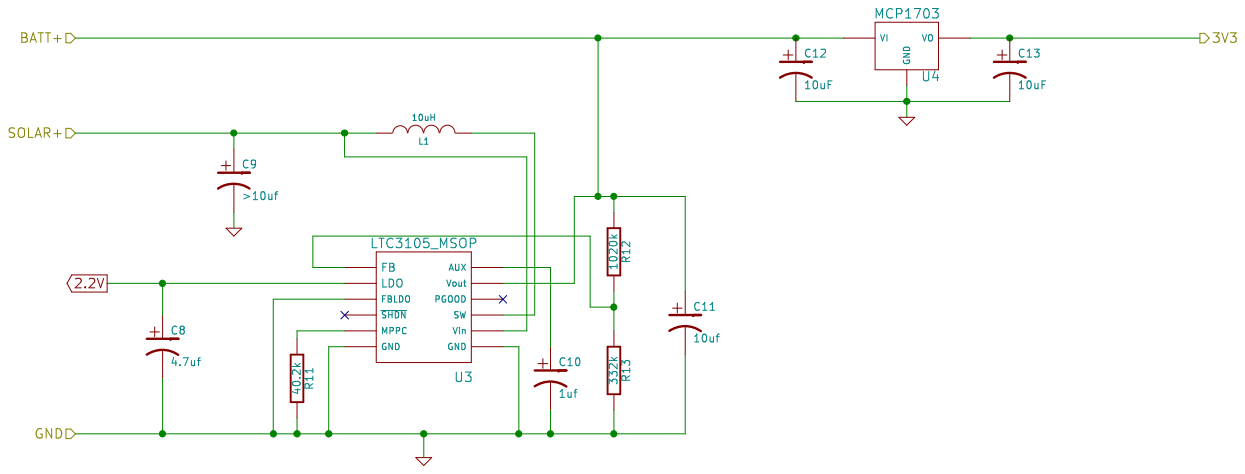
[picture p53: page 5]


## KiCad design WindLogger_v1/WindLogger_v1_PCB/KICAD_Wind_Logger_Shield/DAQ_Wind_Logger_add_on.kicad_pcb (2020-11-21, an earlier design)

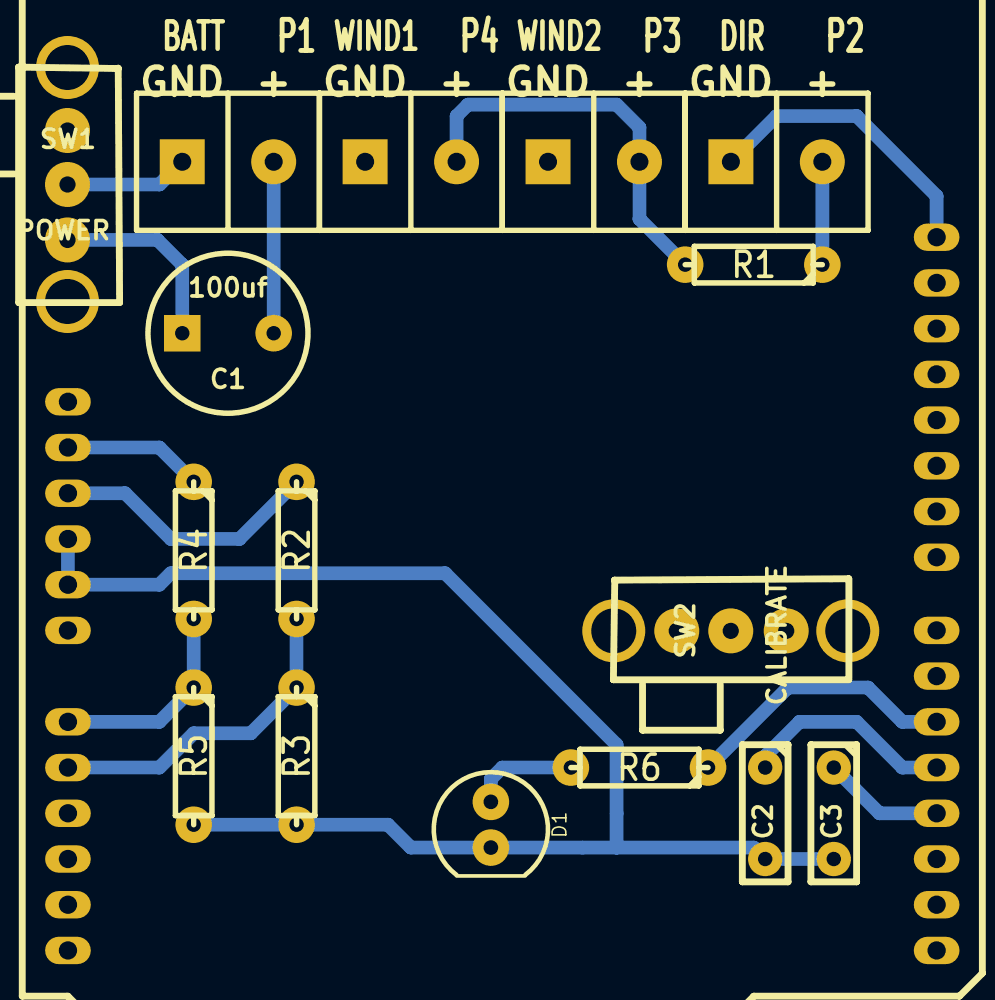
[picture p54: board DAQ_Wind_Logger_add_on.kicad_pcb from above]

Board: 2 copper layers, 17 parts (0 on the bottom side), 12 nets.

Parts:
C1: 100uf; C2V8_large_pad
C2, C3: C; C1_wide_lg_pad_2
D1: DATA; LED-5MM_larg_pad
P1: BATT; SIL-2_screw_terminal
P2: DIR; SIL-2_screw_terminal
P3: WIND2; SIL-2_screw_terminal
P4: WIND1; SIL-2_screw_terminal
R1: 10k; R3-LARGE_PADS_0_8_hole
R2, R3, R4: 47k; R3-LARGE_PADS_0_8_hole
R5: Therm 47k; R3-LARGE_PADS_0_8_hole
R6: 1k; R3-LARGE_PADS_0_8_hole
SHIELD1: ARDUINO_SHIELD; ARDUINO_SHIELD_040pins_no_hole
SW1: POWER; SW_SPDT_rapid_760271
SW2: CALIBRATE; SW_SPDT_rapid_760271

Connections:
+BATT: C1.1, R2.1, SHIELD1.5V, SW1.1
GND: C2.2, C3.2, D1.2, P3.2, P4.2, R1.2, R3.2, R5.2, SHIELD1.GND1, SHIELD1.GND2, SW2.2
unnamed: P1.1, SW1.2
unnamed: SHIELD1.7, SW2.1
unnamed: P2.2, R1.1, SHIELD1.AD2
unnamed: C1.2, P1.2, R2.2, R3.1, SHIELD1.AD1
unnamed: R4.2, R5.1, SHIELD1.AD0
unnamed: P2.1, R4.1, SHIELD1.3V3, SHIELD1.AREF
unnamed: D1.1, R6.2
unnamed: R6.1, SHIELD1.5
unnamed: C2.1, P3.1, SHIELD1.4
unnamed: C3.1, P4.1, SHIELD1.3

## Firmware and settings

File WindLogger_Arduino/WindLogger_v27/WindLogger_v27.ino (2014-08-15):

/********************************************************
/****** Wind Logger based upon the:  ********************
/****** DataDuino - Arduino DAQ UNIT ********************
/****** by Matt Little **********************************
/****** Date: 29/1/2014 *********************************
/****** info@re-innovation.co.uk ************************
/****** www.re-innovation.co.uk *************************
/********************************************************

  See www.re-innovation.co.uk for information and construction details
  
  This is sample code for the DataDuino.

/*************Details of Code*****************************

  The DataDuino is an Arduino based SD card datalogger.
  A PCF8563 Realt Time Clock is used to timestamp the data.
  
  Pin D3 is set up to cound pulses from a sensor (such as a anemometer or flow sensor)
  These are pulses are averaged into a wind speed
  
  Pin A0 is set up to read a thermistor for temperature (GND-47k thermistor - 47k -Vref)
  
  Pin A1 is set up with a 47k/47k potential divider from the input voltage
  
  Pin A2 is set up ro measure wind direction with a 10k resistor to GND (GND-10k-R vane-Vref)
  
  Pin D4 is set up to switch on the power to some IR sensors (for wind direction)
  
  //Pin A1,A2,A3 are set to digital and return data about wind vane direction (NOT IMPLEMENTED YET)
  
  Pin D7 is used as an input to choose calibrate mode
  When in calibrate mode the serial port is read and sample/time/date can be updated
  
  Each logger has a reference (user adjustable).
  
  Data is written to a .csv file created on an SD card.
  A new file is created each day. If file alreay present then data is appended.
  The file name is created from the reference number and the date in the format:
  DXXXXXX.csv, where DXXXXXX is the date in the format DDMMYY. 
  
  Data is stored with human readable headers:
  "Reference, Time, Date, Wind Pulses, Direction, Temp, Humidity"

  // This will be added to a seperate 'calibrate' mode
  When in Calibrate mode:
  You can adjust the parameters of the device using serial commands. These parameters are stored in EEPROM.
  These are:
  T??????E
  This will change the time to HHMMSS
  D??????E
  This will change the date to DDMMYY
  S?????E
  This will change the sample period to ????? seconds. Set to 00001 for 1 second data, set to 03600 for 1 hour data.
  The minimum is 1 second data. The maximum is 99999 seconds
  
  // Addedd Interrupt code from here:
  // PinChangeIntExample, version 1.1 Sun Jan 15 06:24:19 CST 2012
  // See the Wiki at http://code.google.com/p/arduino-pinchangeint/wiki 
  // for more information.
 
  Updates: 
  30/10/12 Code written - Matt Little
  31/10/12 writing code description and sorting out new sample timings - Matt Little
  19/9/13  Getting code to work on Arduino 1.0.5 - Matt Little
  5/2/14   Adding wind logging sections - Matt Little
  5/2/14   Sorting out sleep modes - Matt Little
  5/2/14   Adding HIH humidity/temperature sensor - Matt Little
  5/2/14   Sorting out Card Detect when card removed - Matt Little
  10/2/14  Sorting out card re-enter issue - Matt Little
  17/6/14  Adding pull-up enable for calibrate pin.- Matt Little
  17/6/14  Removing humidity sensor routines. Not needed -  Matt Little
  17/6/14  Adding debounce timer for anemometer pulses - Matt Little
  17/6/14  Adding Direction vane input - Matt Little
  10/7/14  Adding additional Anemometer input - Matt Little
  10/7/14  Needs additional interrupt pin added - Matt Little
  13/8/14  Added wind direction data - Matt Little
  
  TO DO
  Sort out wind direction code - must take reading every second and average.
 
 //*********SD CARD DETAILS***************************	
 The SD card circuit:
 SD card attached to SPI bus as follows:
 ** MOSI - pin 11
 ** MISO - pin 12
 ** CLK - pin 13
 ** CS - pin 10
 ** Card detect - pin 6
 
 //************ Real Time Clock code*******************
 A PCF8563 RTC is attached to pins:
 ** A4 - SDA (serial data)
 ** A5 - SDC (serial clock)
 ** D2 - Clock out - This gives a 1 second pulse to record the data
 
 RTC PCF8563 code details:
 By Joe Robertson, jmr
 orbitalair@bellsouth.net
 
**********************************************************************************************************/


/************ External Libraries*****************************/
//#include <OneWire.h>
//#include <DallasTemperature.h> 
#include <stdlib.h>
#include <Wire.h>          // Required for RTC
#include <Rtc_Pcf8563.h>   // RTC library
#include <SdFat.h>            // SD card library
#include <avr/pgmspace.h>  // Library for putting data into program memory
#include <EEPROM.h>        // For writing values to the EEPROM
#include <avr/eeprom.h>
#include <avr/sleep.h>
#include <avr/power.h>
#include <PinChangeInt.h>  // For additional interrupts

/************User variables and hardware allocation**********************************************/

/******* SD CARD*************/
#define chipSelect 10 // The SD card Chip Select pin 10
#define cardDetect 6  // The SD card detect is on pin 6
// The other SD card pins (D11,D12,D13) are all set within SD.h
int cardDetectOld = LOW;  // This is the flag for the old reading of the card detect

// SD file system object
SdFat sd;
//Log file
SdFile datafile;  

//File datafile;   // The logging file
String dataString;    // This is the holder for the data as a string. Start as blank
int counter = 0;   // Clue is in the name - its a counter.
long dataCounter = 0;  // This holds the number of seconds since the last data store


/*************Real Time Clock*******/
Rtc_Pcf8563 rtc;
#define I2C_RTC 0x51 // 7 bit address (without last bit - look at the datasheet)
#define RTCinterrupt 0  // RTC interrupt - This is pin 2 of ardunio - which is INT0

/************* Pulse counter *******/
#define pulseInterrupt 1  // Pulse Counter Interrupt - This is pin 3 of arduino - which is INT1
#define ANEMOMETER1 3  //   This is digital pin the pulse is attached to
#define ANEMOMETER2 4  //   This is digital pin the pulse is attached to


/********* I/O Pins *************/
#define LEDred 5      // The output led is on pin 5
#define calibrate 7   // This controls if we are in serial calibrate mode or not
#define batteryPin A1  // For monitoring the battery voltage
#define directionPin A2  // For monitoring the wind direction

/********** Wind Direction Storage *************/
String WindDirection = " ";  // Empty to start with
int windDirectionArray[] = {0,0,0,0,0,0,0,0};  //Holds the frequency of the wind direction

/********** Thermistor Data Storage ************/
#define thermistor A0  // This is the analog pin for the thermistor
float TempC = 0;  // This holds the converted value of temperature
char TempCStr[6];  // A string buffer to hold the converted string

// enumarating 3 major temperature scales
enum {
  T_KELVIN=0,
  T_CELSIUS,
  T_FAHRENHEIT
};
// Manufacturer data for episco k164 10k thermistor
// simply delete this if you don't need it
// or use this idea to define your own thermistors
//#define EPISCO_K164_10k 4300.0f,298.15f,10000.0f  // B,T0,R0
//#define GT_Thermistor_10k 4126.0f,298.15f,10000.0f  // B,T0,R0
#define Vishay_Thermistor_47k 4090.0f,298.15f,47000.0f  // B,T0,R0

///********* Thermistor Temperature sensor****************/
float temp;        // Temporary store for float

///********* Battery Voltage ****************/
float batteryVoltage;        // Temporary store for float
char BatteryVoltStr[5];      // Hold the battery voltage as a string

// ****** Serial Data Read***********
// Variables for the serial data read
char inByte;         // incoming serial char
String str_buffer = "";  // This is the holder for the string which we will display

//********Variables for the Filename*******************

char filename[] = "DXXXXXX.csv";  // This is a holder for the full file name
char deviceID[3]; // A buffer to hold the device ID

long sampleTime = 2;  // This is the time between samples for the DAQ
                      // Sample time is stored in EEPROM in locations 2 & 3

// Variables for the Pulse Counter
volatile long pulseCounter1 = 0;  // This counts pulses from the flow sensor  - Needs to be long to hold number
volatile long pulseCounter1Old = 0;  // This is storage for the old flow sensor - Needs to be long to hold number

volatile long pulseCounter2 = 0;  // This counts pulses from the flow sensor  - Needs to be long to hold number
volatile long pulseCounter2Old = 0;  // This is storage for the old flow sensor - Needs to be long to hold number

volatile boolean writedataflag = HIGH;  // A flag to tell the code when to write data

// Varibales for writing to EEPROM
int hiByte;      // These are used to store longer variables into EERPRPROM
int loByte;

// These next ints are for the filename conversion
int day_int =0;      // To find the day from the Date for the filename
int day_int1 =0;
int day_int2 =0;
int month_int = 0;
int month_int1 = 0;
int month_int2 = 0;
int year_int = 0;  // Year
int hour_int = 0;
int min_int = 0;
int sec_int = 0;

boolean calibrateFlag = HIGH;  // This flag is lowered if we are in calibrate mode (switch ON)
boolean debugFlag = LOW;    // Set this if you want to be in debugging mode.

//**********STRINGS TO USE****************************
String comma = ",";
String date;        // The stored date from filename creation
String newdate;     // The new date, read every time 

// These are Char Strings - they are stored in program memory to save space in data memory
// These are a mixutre of error messages and serial printed information
const char headers[] PROGMEM = "Reference, Date, Time, Wind1, Wind2, Direction, Thermistor, Battery Voltage";  // Headers for the top of the file
const char headersOK[] PROGMEM = "Headers OK";
const char erroropen[] PROGMEM = "Error opening file";
const char error[] PROGMEM = "ERROR ERROR ERROR";
const char initialisesd[] PROGMEM = "Initialising SD card...";
const char dateerror[] PROGMEM = "Dates are not the same - create new file";
const char reference[] PROGMEM = "The ref number is:";
const char noSD[] PROGMEM = "No SD card present";

#define MAX_STRING 80      // Sets the maximum length of string probably could be lower
char stringBuffer[MAX_STRING];  // A buffer to hold the string when pulled from program memory

/***************************************************
 *  Name:        pulse1
 *
 *  Returns:     Nothing.
 *
 *  Parameters:  None.
 *
 *  Description: Count pulses from Anemometer 1
 *
 ***************************************************/
void pulse1(void)
{
  // If the anemometer has spun around
  // Increment the pulse counter
  pulseCounter1++;
  // ***TO DO**** Might need to debounce this
}

/***************************************************
 *  Name:        pulse2
 *
 *  Returns:     Nothing.
 *
 *  Parameters:  None.
 *
 *  Description: Count pulses from Anemometer 2
 *
 ***************************************************/
void pulse2(void)
{
  // If the anemometer has spun around
  // Increment the pulse counter
  pulseCounter2++;
  // ***TO DO**** Might need to debounce this
}

/***************************************************
 *  Name:        RTC
 *
 *  Returns:     Nothing.
 *
 *  Parameters:  None.
 *
 *  Description: I use the CLK_OUT from the RTC to give me exact 1Hz signal
 *               To do this I changed the initialise the RTC with the CLKOUT at 1Hz
 *
 ***************************************************/
void RTC()
{ 
  detachInterrupt(RTCinterrupt);
  dataCounter++;

  if(writedataflag==LOW&&dataCounter>=sampleTime)  // This stops us loosing data if a second is missed
  { 
    // If this interrupt has happened then we want to write data to SD card:
    // Save the pulsecounter value (this will be stored to write to SD card
    pulseCounter1Old = pulseCounter1;
    pulseCounter2Old = pulseCounter2;
   // Reset the pulse counter
    pulseCounter1 = 0;
    pulseCounter2 = 0;
    // Reset the DataCounter
    dataCounter = 0;  
    // Set the writedataflag HIGH
    writedataflag=HIGH;
  }
}

/***************************************************
 *  Name:        enterSleep
 *
 *  Returns:     Nothing.
 *
 *  Parameters:  None.
 *
 *  Description: Enters the arduino into sleep mode.
 *
 ***************************************************/
void enterSleep(void)
{

  attachInterrupt(RTCinterrupt, RTC, RISING);
  
  sleep_enable();
   
  set_sleep_mode(SLEEP_MODE_PWR_DOWN);  
  
  byte old_ADCSRA = ADCSRA;  // Store the old value to re-enable 
  // disable ADC
  ADCSRA = 0;

  byte old_PRR = PRR;  // Store previous version on PRR
  // turn off various modules
  PRR = 0b11111111;
  
  sleep_cpu();
  /* The program will continue from here. */
  /************* ASLEEP *******************/
  
  // ZZZZZZZZZZZZZZZZZZZZZZZZZZZZZZZZZZZZ //
  
  /************** WOKEN UP ***************/
  /* First thing to do is disable sleep. */
  sleep_disable();
  
  // turn ON various modules USART and ADC
  PRR = old_PRR;  
  
  // enable ADC
  ADCSRA = old_ADCSRA;  
}


/***************************************************
 *  Name:        setup
 *
 *  Returns:     Nothing.
 *
 *  Parameters:  None.
 *
 *  Description: Setup for the Arduino.           
 *
 ***************************************************/
void setup()
{
  Serial.begin(115200);
  Wire.begin();
  
  //******Real Time Clock Set - up********
  // A4 and A5 are used as I2C interface.
  // D2 is connected to CLK OUT from RTC. This triggers an interrupt to take data
  // We need to enable pull up resistors
  pinMode(A4, INPUT);           // set pin to input
  digitalWrite(A4, HIGH);       // turn on pullup resistors
  pinMode(A5, INPUT);           // set pin to input
  digitalWrite(A5, HIGH);       // turn on pullup resistors
  pinMode(2,INPUT);    // Set D2 to be an input for the RTC CLK-OUT   
  //initialise the real time clock
  Rtc_Pcf8563 rtc; 

  //initialisetemp();  // Initialise the temperature sensors
  pinMode(LEDred,OUTPUT);    // Set D5 to be an output LED
  pinMode(cardDetect,INPUT);  // D6 is the SD card detect on pin 6.
 
  //Set up digital data lines
  pinMode(calibrate,INPUT_PULLUP);
 
  // Battery voltage sensing
  pinMode(batteryPin,INPUT);
  
   //Set up direction input for wind vane
  pinMode(directionPin,INPUT); 
  
  // Put unused pins to INPUT to try and save power...   
  pinMode(9,INPUT);    
  pinMode(A3,INPUT); 
  
  setupRTC();  // Initialise the real time clock  
  
  initialiseSD();    // Inisitalise the SD card   
  createfilename();  // Create the corrct filename (from date)

  // Read the reference number from the EEROM
  deviceID[0] = char(EEPROM.read(0));
  deviceID[1] = char(EEPROM.read(1));
  
  // Read in the sample time from EEPROM
  hiByte = EEPROM.read(2);
  loByte = EEPROM.read(3);
  sampleTime = (hiByte << 8)+loByte;  // Get the sensor calibrate value 
  
  analogReference(EXTERNAL);  // This should be default, but just to be sure

  // Interrupt for the 1Hz signal from the RTC
  attachInterrupt(RTCinterrupt, RTC, RISING); 
  // Attach interrupts for the pulse counting
  pinMode(ANEMOMETER1, INPUT); 
  digitalWrite(ANEMOMETER1, HIGH);
  PCintPort::attachInterrupt(ANEMOMETER1, &pulse1, FALLING);  // add more attachInterrupt code as required
  pinMode(ANEMOMETER2, INPUT); 
  digitalWrite(ANEMOMETER2, HIGH);
  PCintPort::attachInterrupt(ANEMOMETER2, &pulse2, FALLING);  
 
}


/***************************************************
 *  Name:        main loop
 *
 *  Returns:     Nothing.
 *
 *  Parameters:  None.
 *
 *  Description: Main application loop.
 *
 ***************************************************/
void loop()
{

  // *********** WIND DIRECTION **************************************  
  // Want to measure the wind direction every second to give good direction analysis
  // This can be checked every second and an average used
  convertWindDirection(analogRead(directionPin));    // Run this every second. It increments the windDirectionArray 
  
  if(writedataflag==HIGH)
  {  
    pinMode(LEDred,OUTPUT);    // Set LED to be an output LED 
    digitalWrite(LEDred, HIGH);   // set the LED ON

    // *********** WIND SPEED ******************************************
    // Want to get the number of pulses and average into the sample time
    // This gives us the average wind speed
    // pulsecounterold holds the value of pulses.
    // This can be converted into the wind speed using the time and 
    // the pulse-wind speed characterisitic of the anemometer.
    // Do this as post processing - pulse count is most important.
    
    // *********** WIND DIRECTION **************************************
    // This can be checked every second and an average used
    WindDirection = analyseWindDirection();
    for(int i=0;i<8;i++)
    {
      //Resets the wind direction array
      windDirectionArray[i]=0;
    }
 
    // *********** TEMPERATURE *****************************************
    // Two versions of this - either with thermistor or I2C sensor (if connected)
    // Thermistor version
    // Get the temperature readings and store to variables
    TempC = Temperature(thermistor,T_CELSIUS,Vishay_Thermistor_47k,47000.0f);
    dtostrf(TempC,2,2,TempCStr);  // Convert the temperature value (double) into a string
    
    if(debugFlag==HIGH)
    {
      Serial.print("Therm: ");
      Serial.println(TempCStr);  
    }   

    // *********** BATTERY VOLTAGE ***************************************
    // From Vcc-47k--47k-GND potential divider
    // This is to test in case battery voltage has dropped too low - alert?
    batteryVoltage = float(analogRead(batteryPin))*(3.3/1024.0)*2.0;        // Temporary store for float
    dtostrf(batteryVoltage,2,2,BatteryVoltStr);     // Hold the battery voltage as a string
    
    // ******** put this data into a file ********************************
    // ****** Check filename *********************************************
    // Each day we want to write a new file.
    // Compare date with previous stored date, every second
    newdate = String(rtc.formatDate(RTCC_DATE_WORLD));  
    if(newdate != date)
    {
       // If date has changed then create a new file
       createfilename();  // Create the corrct filename (from date)
    }    

    // ********* Create string of data **************************
    dataString =  String(deviceID[0]); 
    dataString += deviceID[1];  // Reference
    dataString += comma;
    dataString += newdate;  // Date
    dataString += comma;
    dataString += String(rtc.formatTime()); // Time
    dataString += comma;
    dataString += String(pulseCounter1Old); // Wind pulses 1
    dataString += comma;
    dataString += String(pulseCounter2Old); // Wind pulses 2
    dataString += comma;
    dataString += WindDirection; // Wind direction
    dataString += comma;
    dataString += TempCStr;  // Temperature (Thermistor)
    dataString += comma;
    dataString += BatteryVoltStr;  // Battery voltage  
    
    // ************** Write it to the SD card *************
    // This depends upon the card detect.
    // If card is there then write to the file
    // If card has recently been inserted then initialise the card/filenames
    // If card is not there then flash LEDs

    if(digitalRead(cardDetect)==LOW&&cardDetectOld==HIGH)
    {
      delay(100);  // Wait for switch to settle down.
      // There was no card previously so re-initialise and re-check the filename
      initialiseSD();
      createfilename();
    }
    if(digitalRead(cardDetect)==LOW&&cardDetectOld==LOW)
    {
      //Ensure that there is a card present)
      // We then write the data to the SD card here:
      writetoSD();
    }
    else
    {
       Serial.println(getString(noSD));
    }   
    cardDetectOld = digitalRead(cardDetect);  // Store the old value of the card detect
    
    // Finish up write routine here:    
    digitalWrite(LEDred, LOW);   // set the LED OFF 
    pinMode(LEDred,INPUT);    // Set LED to be an INPUT - saves power   
    writedataflag=LOW;
    Serial.flush();    // Force out the end of the serial data
  }
  
  // Want to check the SD card every second
  if(digitalRead(cardDetect)==HIGH)
  {
    pinMode(LEDred,OUTPUT);    // Set LED to be an output LED 
    // This meands there is no card present so flash the LED every second
    for(int x=0;x<=5;x++)
    {
      digitalWrite(LEDred, HIGH);   // set the LED ON
      delay(5);
      digitalWrite(LEDred, LOW);   // set the LED ON
      delay(50);     
    }
  } 
    
  if(debugFlag==HIGH)
  {
    // DEBUGGING ONLY........
    Serial.print("Anemometer1: ");
    Serial.println(pulseCounter1, DEC);
    Serial.print("Anemometer2: ");
    Serial.println(pulseCounter2, DEC);
  }
  
  // A Switch on D7 will set if the unit is in serial adjust mode or not  
  //calibrateFlag = digitalRead(calibrate);  
  
  if(digitalRead(calibrate)==LOW)
  {    
    // We ARE in calibrate mode
    Serial.println("Calibrate");    
    getData();
    delay(500);  // Some time to read data
    Serial.flush();    // Force out the end of the serial data
  
    // Reset all the data collection values
    WindDirection = analyseWindDirection();
    Serial.print("Vane Direction:");
    Serial.println(WindDirection);
    
    for(int i=0;i<8;i++)
    {
      //Resets the wind direction array
      windDirectionArray[i]=0;
    }
    pulseCounter1 = 0;
    pulseCounter2 = 0;
    dataCounter = 0;  
    writedataflag=LOW;
  }
  else
  {     
    attachInterrupt(RTCinterrupt, RTC, RISING); 
    enterSleep();     
  }
  
}
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

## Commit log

2014-08-15 Update 15/8/14
    New Arduino code. Updated PCB. Updated Instructions
2014-08-15 Arduino code update
2014-10-29 Update with Instructions
    Put in different language instructions
    [2_10_14_Wind_Logger_Anemometer_Fixing_no_measurements.dxf]
2020-11-21 Large update and rearrange of windlogger files
    Added both version 1 and version 3.
    [2_10_14_Wind_Logger_Anemometer_Fixing_no_measurements.dxf, ArduinoUno.sch, DAQ_Flow_LEEDR_v4.brd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]
